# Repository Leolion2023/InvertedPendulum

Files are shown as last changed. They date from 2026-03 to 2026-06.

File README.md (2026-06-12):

# InvertedPendulum
## Concept Idea
A small robot capable of balancing itself so that it remains upright despite having only two wheels.
The motivation behind this is a school project, with the main focus on self-regulating control loops. This robot was our idea for the project.

---

## Language
- Primary Documentation (English): [README.md](README.md)
- German Version: [README.de.md](README.de.md)

---

## Table of Contents

1. [Hardware](#hardware)
   1. [Requirements](#requirements)
   2. [Pinout](#pinout)
   3. [Schematic](#schematic)
   4. [Breadboard](#breadboard)
2. [Software](#software)
   1. [Code](#code)
   2. [Control Loop Diagram](#control-loop-diagram)
   3. [Program Flowchart](#program-flowchart)
3. [Operating Instructions](#operating-instructions)

---

## To Do

- [x] Create a CAD model of the robot
- [x] Make component connections more stable (based on 3 prototypes to ensure maximum reliability, see [Prototypes](/assets/Prototypes.jpg))
- [x] Design for resource efficiency
- [x] Use fewer components for easier assembly and more stable holding
- [x] Fixed sensor mounting on the PCB for stable readings
- [x] Design non-slip tires
- [x] Reuse PCB from an old project to recycle resources
- [x] Write code to keep the robot upright
- [ ] Improve code to enable calibration via smartphone
   - [ ] Connect via BLE to an app **OR**
   - [ ] Open a web server on the local Wi-Fi network
- [ ] Prevent slight tilting
   - Could be related to PID control (unable to compensate for small angles¹)
- [ ] Consider additional parameters in control
   - For example, preventing the robot from covering large distances (or doing so intentionally). Additionally, unintended rotation could be compensated for or controlled.

**Notes:**
1. The code prevents the system from reacting to small angles. However, testing without this hysteresis also failed, as a ~1-2 degree angle only results in a few watts of output to the motor, which is insufficient for compensation. An adjustment should be written to react more aggressively to small values.

## Updates

`
In the first version of the model, the joints were equipped with sliders. These were intended to simplify assembly, but unfortunately it quickly became apparent that they came apart too easily when subjected to even a little too much force. We resolved this issue by designing new joints that were significantly more stable and in which all degrees of freedom were locked in place by a snap-fit mechanism. We also combined various smaller components into larger assemblies, which also provided greater stability. The old versions can be viewed in the Git history. 
`

---

# Hardware
## Requirements

- 2 x geared motors ~600 RPM
   - 2 x M3 screws, 7.3 mm (flat head/countersunk¹)
- ESP32
- BNO055 9DoF Sensor²
- H-Bridge (e.g., HW-095 L298N)
- CAD 3D-printed parts ([see here](TechDrawRework.pdf))³

**Notes:**
1. The screw type depends on the geared motor used.
2. We used this [self-created wiki](https://github.com/Leolion2023/BNO055) because the Bosch documentation is difficult to understand.
3. If you have issues displaying the technical drawing, please download the file and open it in a modern PDF viewer.

---
## Pinout

| ESP32 Pin | Function | Additional Info |
|---|---|---|
| GPIO16 | H-Bridge IN1 | Used for Motor 1 |
| GPIO17 | H-Bridge IN2 | Used for Motor 1 |
| GPIO23 | H-Bridge ENA | Used for Motor 1 (PWM) |
| GPIO18 | H-Bridge IN3 | Used for Motor 2 |
| GPIO19 | H-Bridge IN4 | Used for Motor 2 |
| GPIO33 | H-Bridge ENB | Used for Motor 2 (PWM) |
| GPIO21 | BNO055 SDA | |
| GPIO22 | BNO055 SCL | |
| 3.3V | BNO055 VIN | |
| GND | BNO055 GND | |
| GND | BNO055 ADD | |
| --- | BNO055 INT | *Not used* |
| --- | BNO055 RST | *Not used* |
| --- | BNO055 BOOT | *Not used* |

---
## Schematic
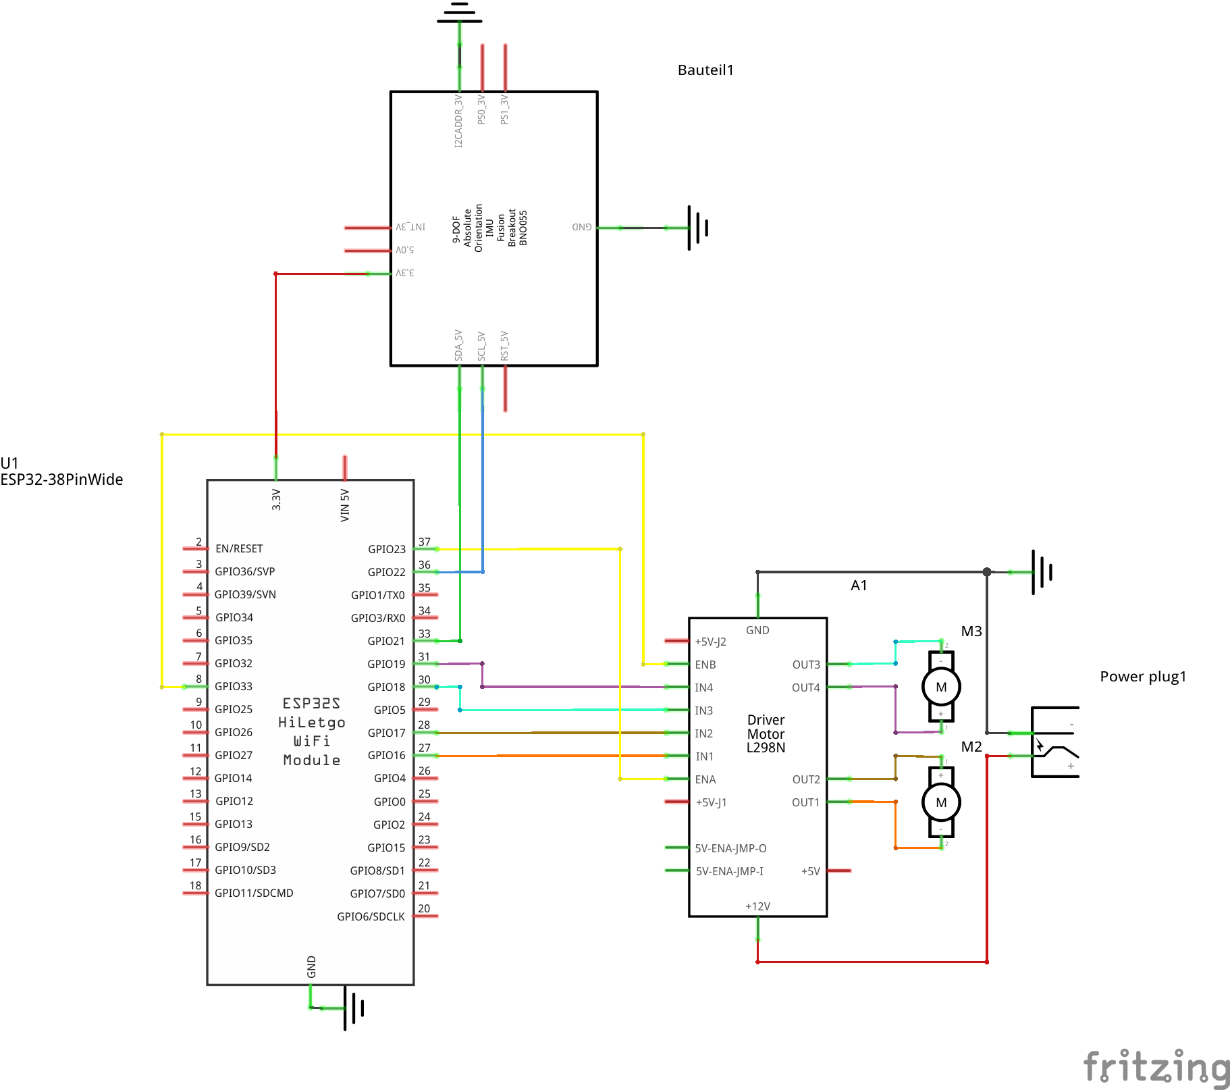
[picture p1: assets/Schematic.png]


---
## Breadboard
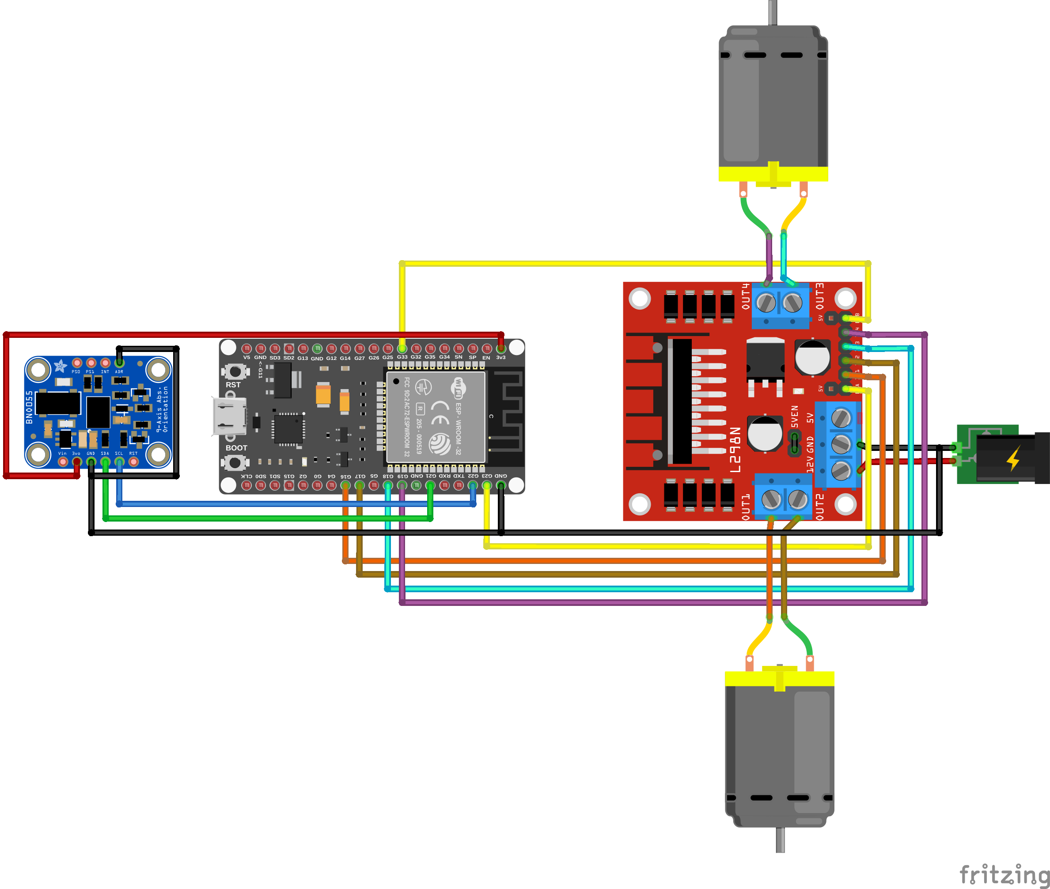
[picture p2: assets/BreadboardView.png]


---
# Software

---
## Code
The main code is located in [src/src/main.cpp](src/src/main.cpp).
We used PlatformIO to flash the ESP32. Adjust as needed to fit your requirements.

---
## Control Loop Diagram
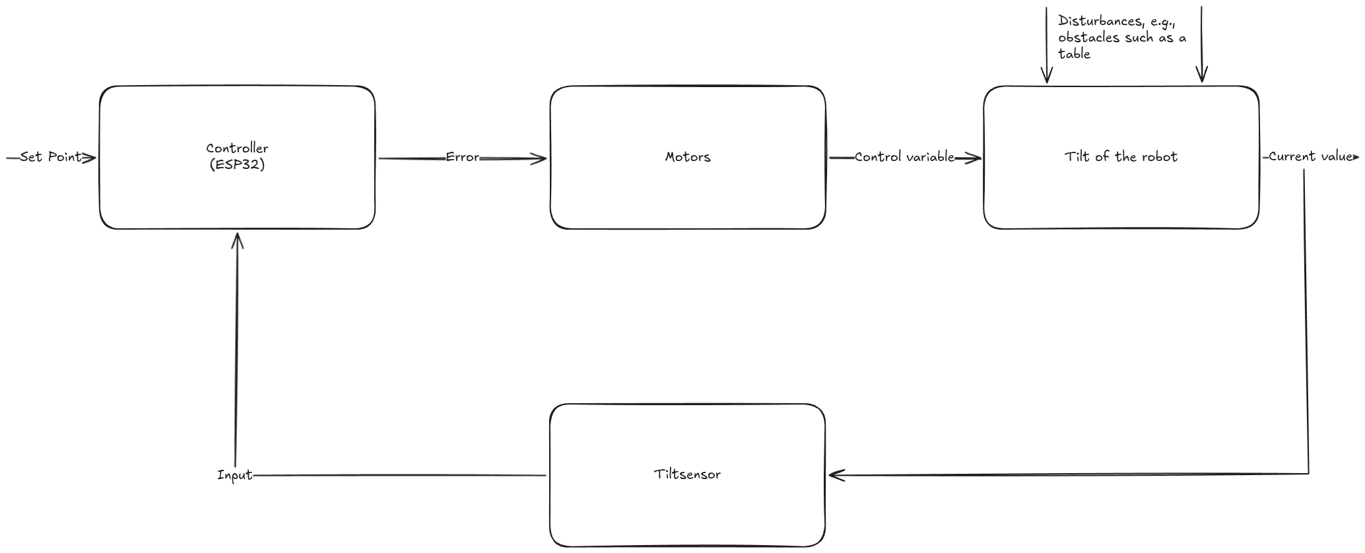
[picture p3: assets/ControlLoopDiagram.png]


---
## Program Flowchart
Currently only available in German.

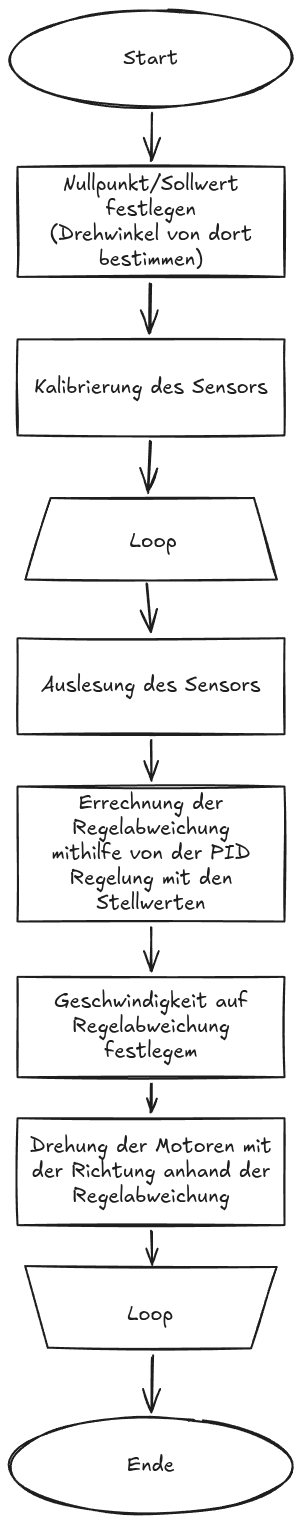
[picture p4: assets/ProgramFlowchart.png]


**Both diagrams were created using [excalidraw.com](https://excalidraw.com).**

---
# Operating Instructions

---
### Electrical Startup

The robot requires two separate power supplies: one for logic voltage and one for motor voltage. The logic voltage can be provided via the ESP32’s USB-C port, the VIN pin (3.3V–5V), or the 3.3V pin. However, we recommend using the connector on the PCB directly next to the ESP32. The motor voltage must be connected either directly to the H-Bridge at the 12V and GND terminals or to the main power supply on the PCB.

Since you will likely need to calibrate the PID values, the easiest way is to connect the ESP32 to a computer with either PlatformIO or the Arduino IDE installed:

**For PlatformIO:**
1. Install PlatformIO on your laptop/PC/etc.
2. Install the custom library for BNO055 (linked above) or the official Bosch library (no guarantee of updates).
3. Adjust the code as described in the next section.
4. Place the robot on a level surface so the wheels are not touching the ground (for initial calibration).
5. Connect the ESP32 and upload the code.

**For Arduino IDE:**
1. Install Arduino IDE.
2. Install the library ([either via Arduino Library Manager or as a file](https://docs.arduino.cc/software/ide-v1/tutorials/installing-libraries/)).
3. Adjust the code as described in the next section.
4. Place the robot on a level surface so the wheels are not touching the ground (for initial calibration).
5. Connect the ESP32 and upload the code.

---
### Code Adjustments

There are a few simple adjustments to be made. At the top, you’ll find the three PID constants, which need to be tuned for your robot. The `constraint` limits the maximum output of the PID controller. Typically, 255.0 is reasonable, as it is the maximum PWM value. The `minConstraint` prevents the motors from spinning at low power, as rapid toggling of the power supply can damage the motors. The `inverted` variable controls the motor rotation direction. If the robot regulates in the wrong direction, change it to `-1.0` or `1.0`.

---
### Hardware Information

To build the robot, you can simply use the technical drawings. Minor adjustments to the variables in the CAD files can improve the connections but may also introduce errors.

**Notes:**
1. We currently have the motors connected in parallel to one channel of the H-Bridge, as they otherwise rotated differently. This could also be balanced by code that reads the other dimensions of the BNO055 and attempts to prevent rotation.

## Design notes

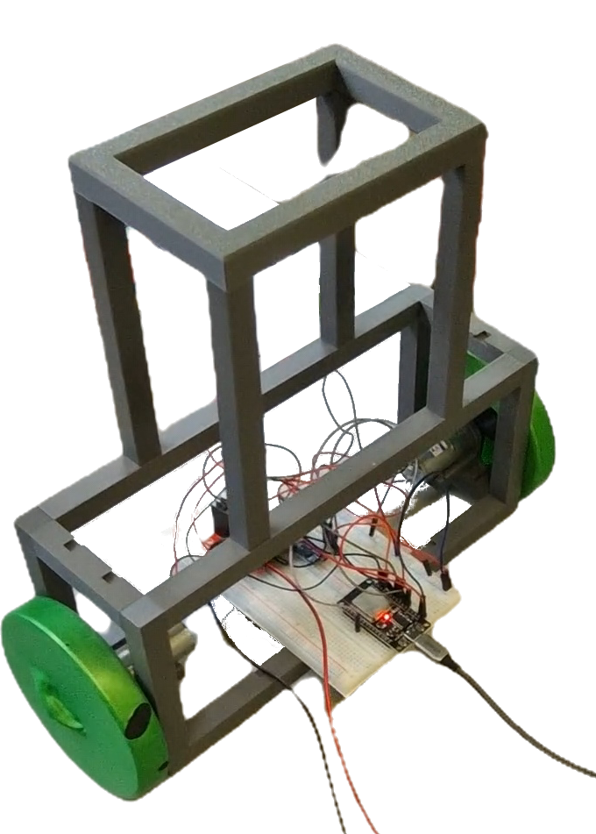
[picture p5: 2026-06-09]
assets/MK1.png

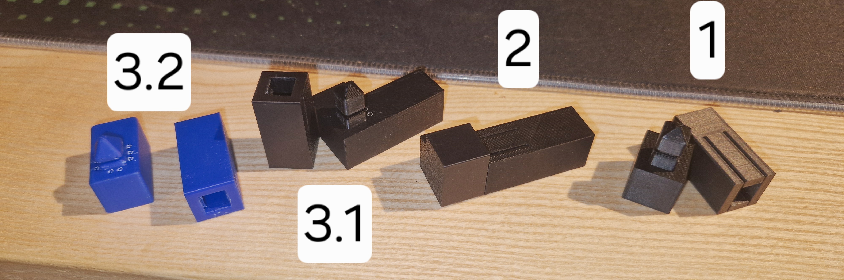
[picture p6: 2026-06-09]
assets/Prototypes.jpg

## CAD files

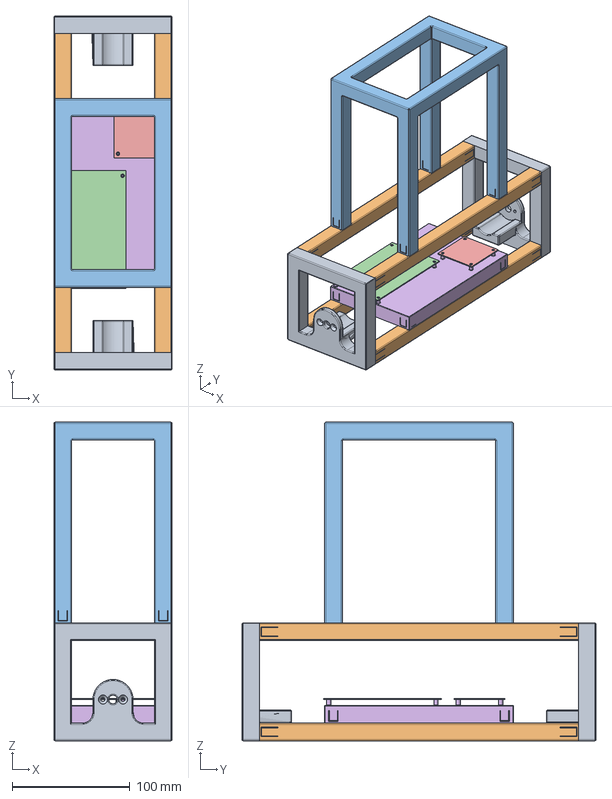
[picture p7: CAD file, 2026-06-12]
CAD/NewSetup.FCStd
100.0 x 300.0 x 270.0 mm
SidePanel001 x 2
Beam001 x 4
Top
PCB
L298N
PCBHolder

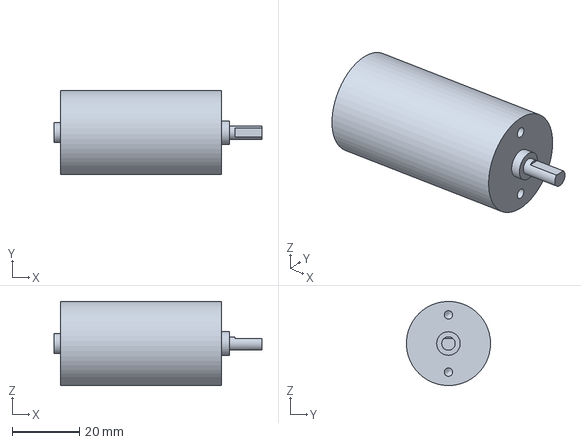
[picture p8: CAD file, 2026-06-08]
CAD/DCMotor.FCStd
61.8 x 25.0 x 25.0 mm

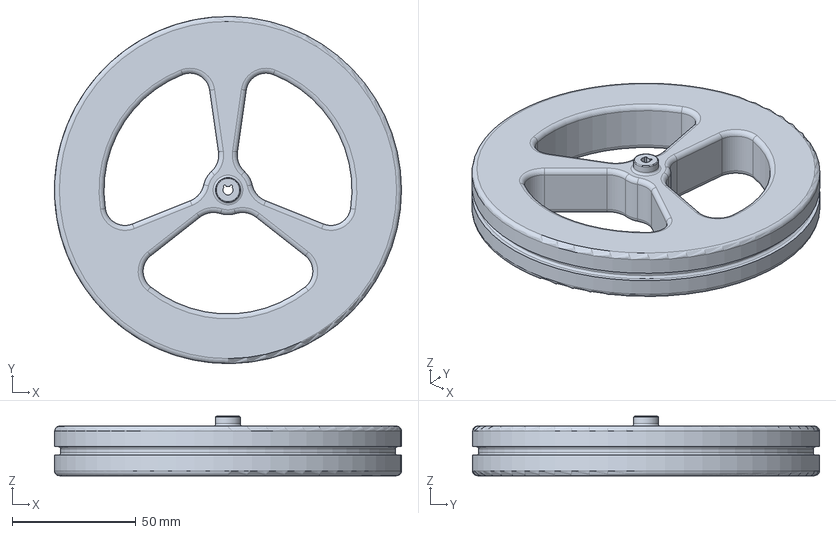
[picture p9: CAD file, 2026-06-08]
CAD/Wheel.FCStd
140.0 x 140.0 x 24.0 mm

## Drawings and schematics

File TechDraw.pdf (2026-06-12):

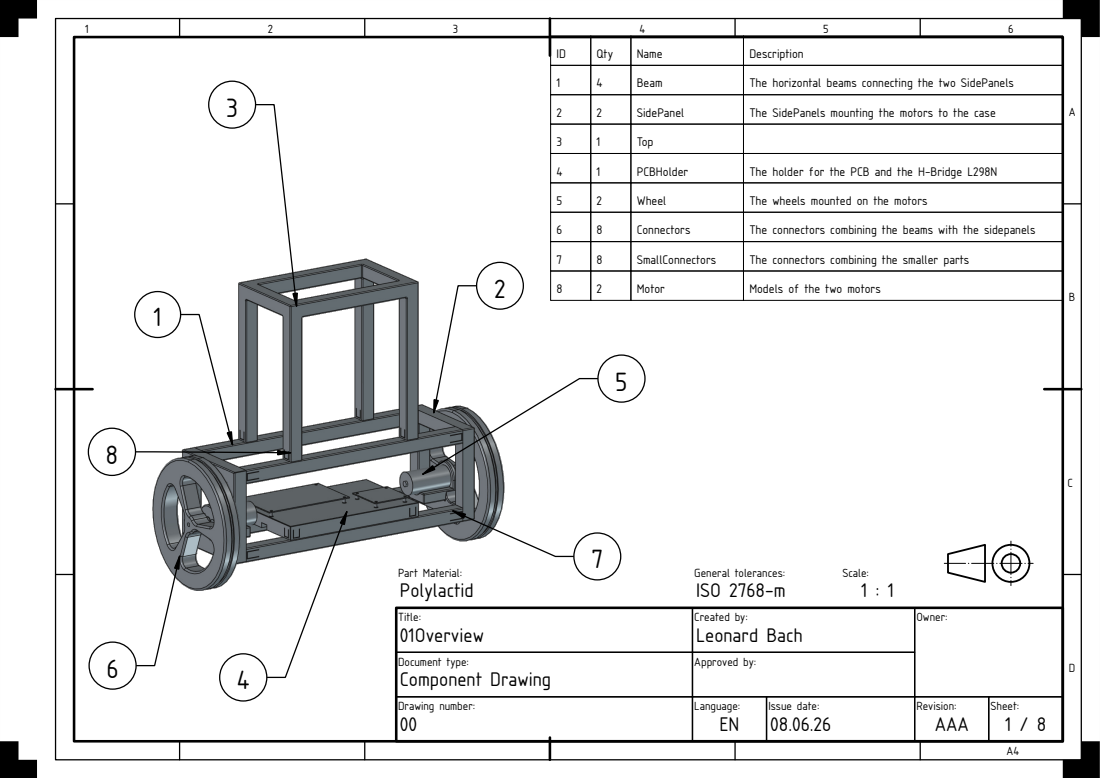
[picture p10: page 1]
Part Material:; General tolerances:; Scale:; Polylactid; ISO 2768-m

ID | Qty | Name | Description
1 | 4 | Beam | The horizontal beams connecting the two SidePanels
2 | 2 | SidePanel | The SidePanels mounting the motors to the case
3 | 1 | Top
4 | 1 | PCBHolder | The holder for the PCB and the H-Bridge L298N
5 | 2 | Wheel | The wheels mounted on the motors
6 | 8 | Connectors | The connectors combining the beams with the sidepanels
7 | 8 | SmallConnectors | The connectors combining the smaller parts
8 | 2 | Motor | Models of the two motors

Title: 01Overview | Created by: Leonard Bach | Owner:

Document type: Component Drawing | Approved by:

Drawing number: 00 | Language: EN | Issue date: 08.06.26 | Revision: AAA | Sheet: 1 / 8

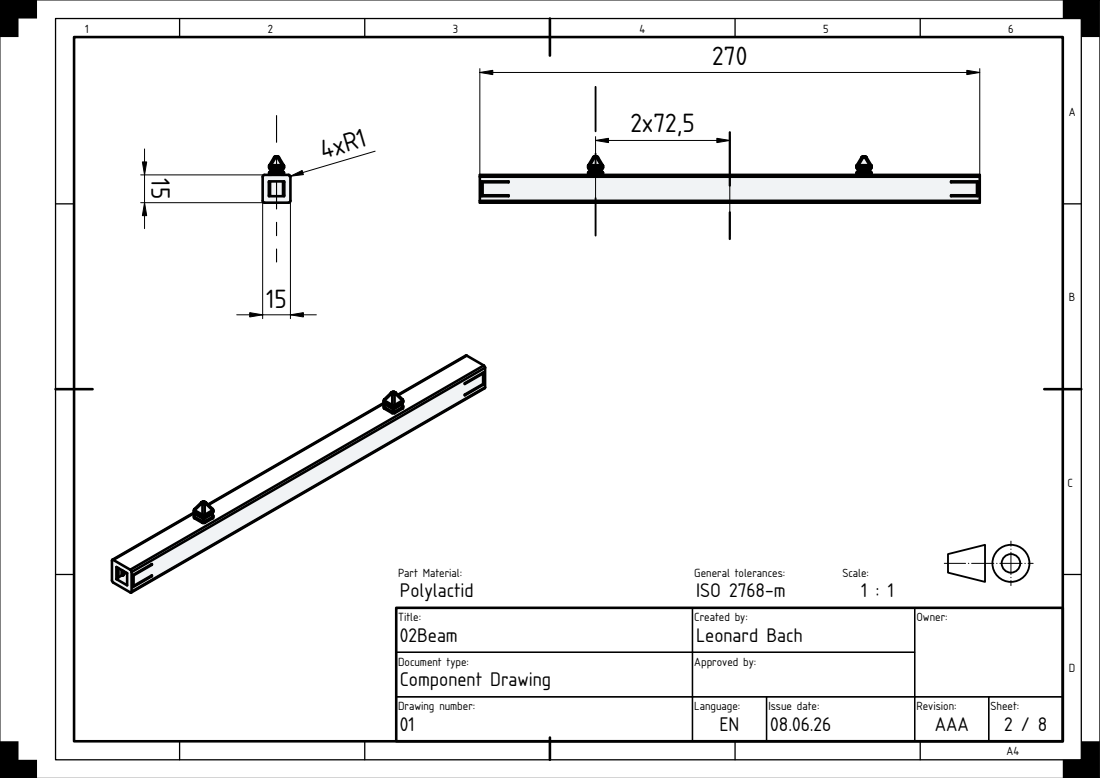
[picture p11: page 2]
Part Material:; General tolerances:; Scale:; Polylactid; ISO 2768-m

Title: 02Beam | Created by: Leonard Bach | Owner:

Document type: Component Drawing | Approved by:

Drawing number: 01 | Language: EN | Issue date: 08.06.26 | Revision: AAA | Sheet: 2 / 8

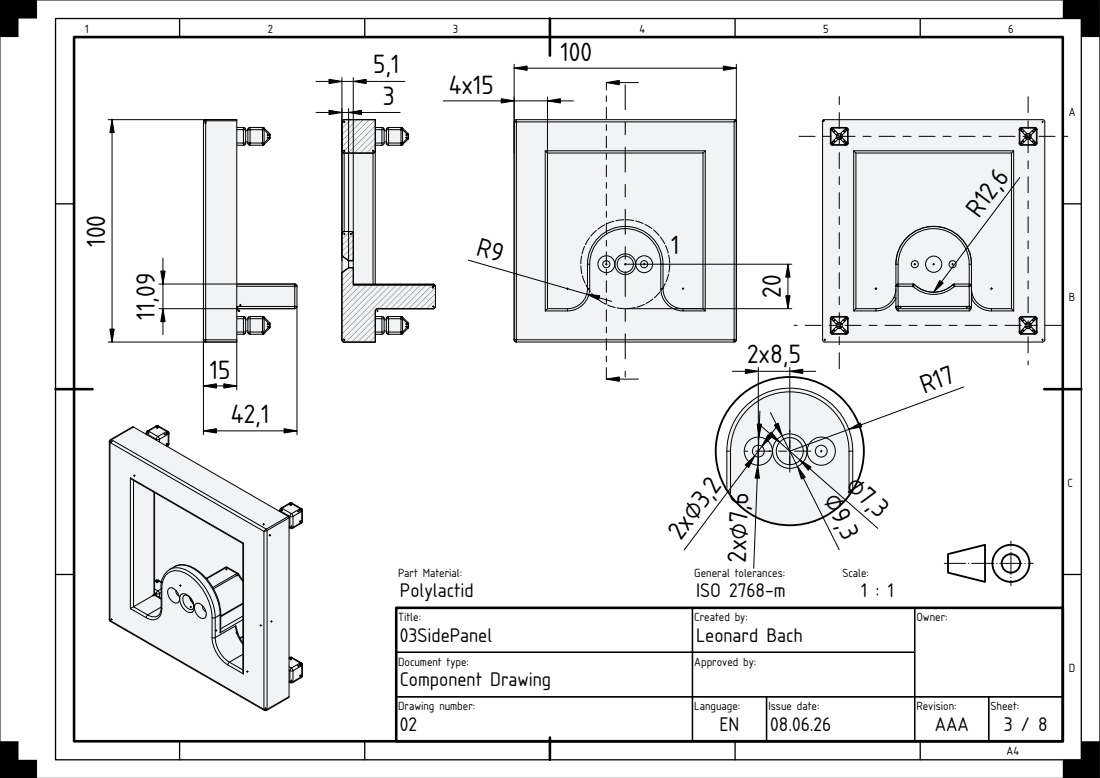
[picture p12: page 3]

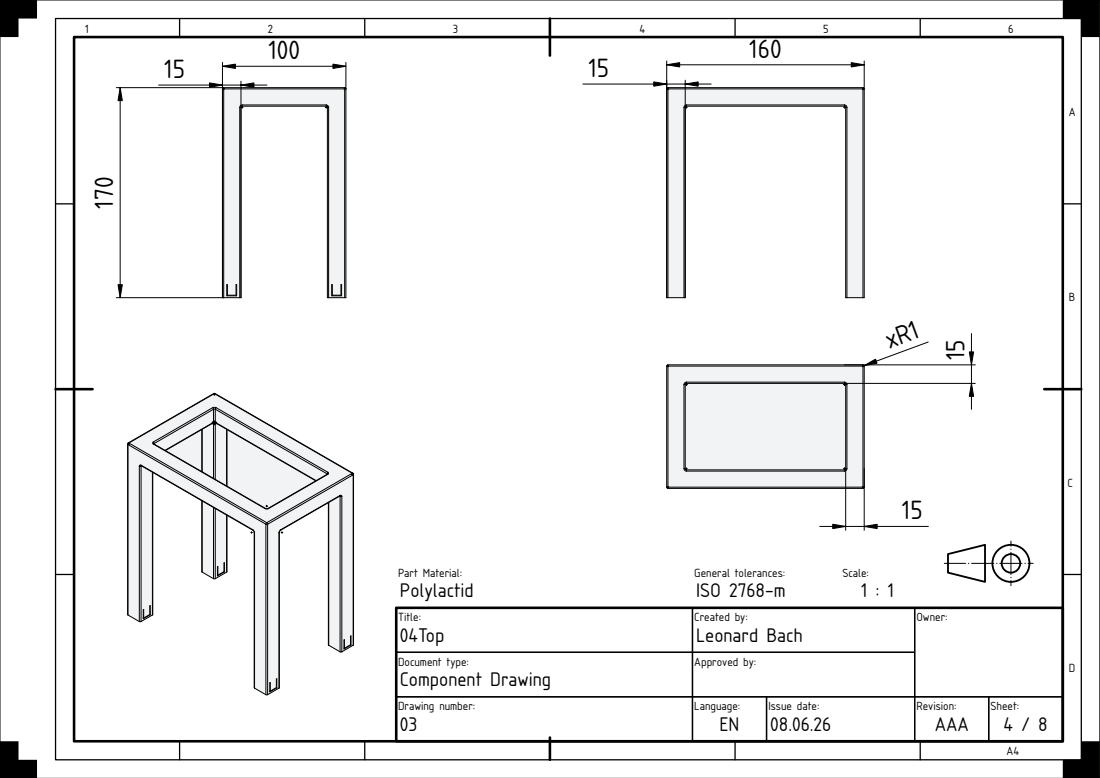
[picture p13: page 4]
Part Material:; General tolerances:; Scale:; Polylactid; ISO 2768-m

Title: 04Top | Created by: Leonard Bach | Owner:

Document type: Component Drawing | Approved by:

Drawing number: 03 | Language: EN | Issue date: 08.06.26 | Revision: AAA | Sheet: 4 / 8

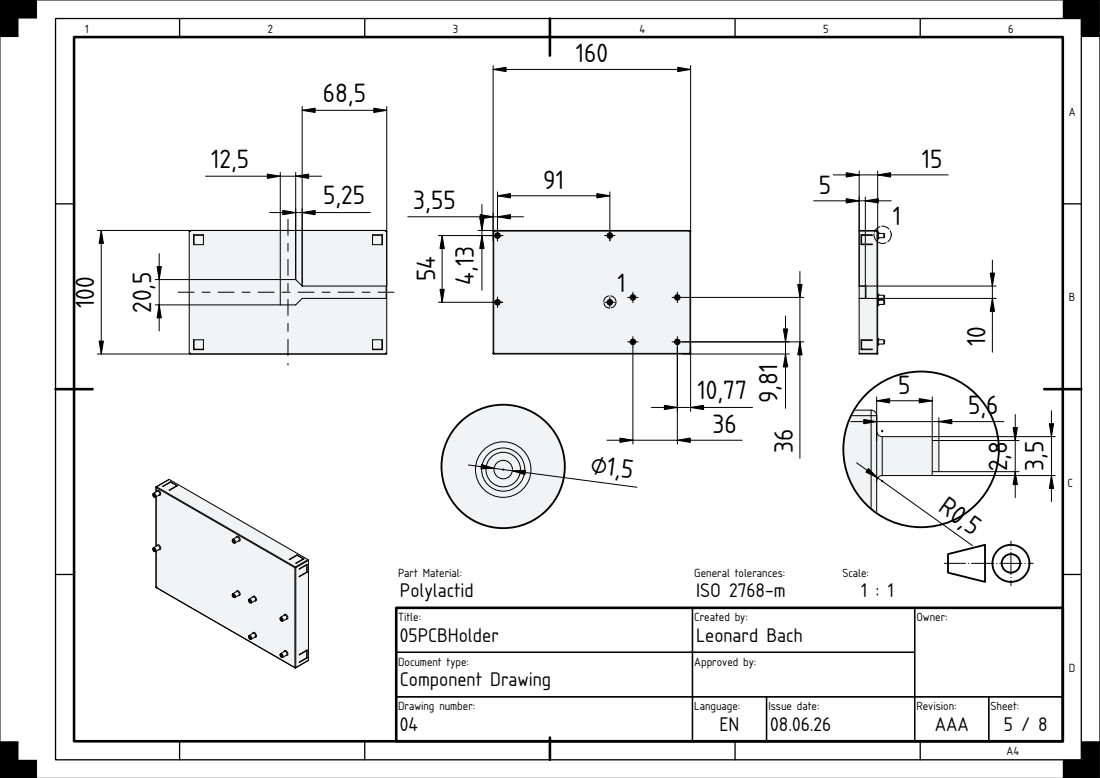
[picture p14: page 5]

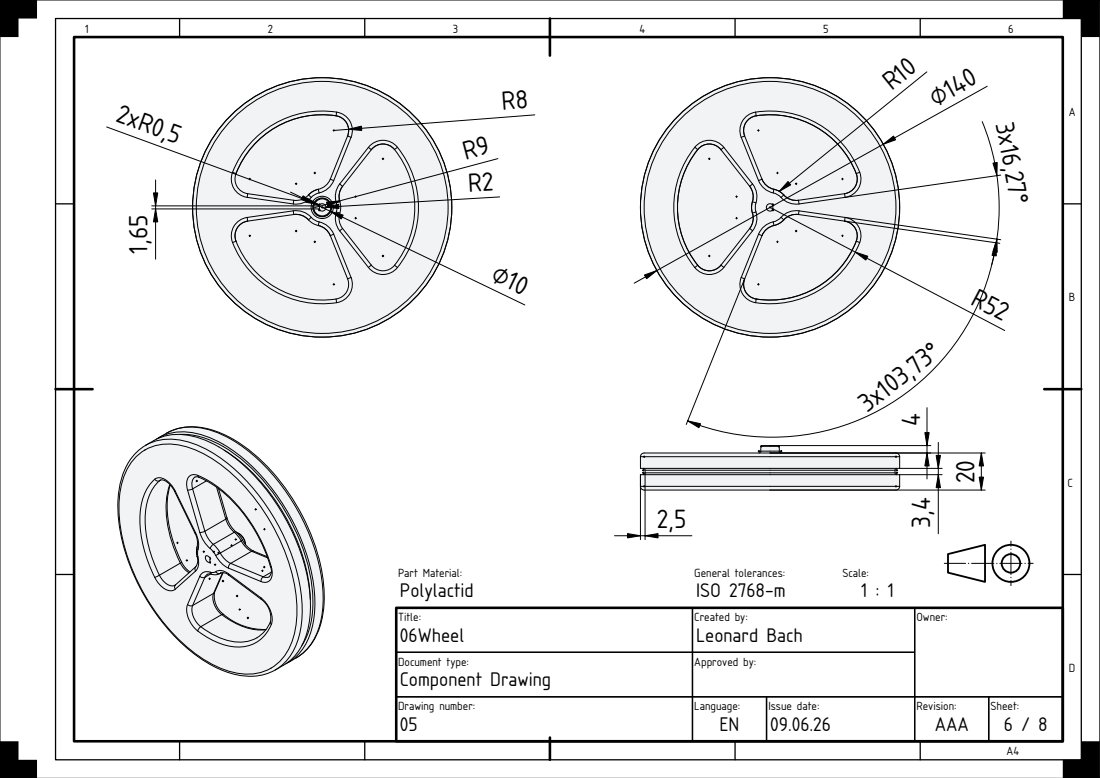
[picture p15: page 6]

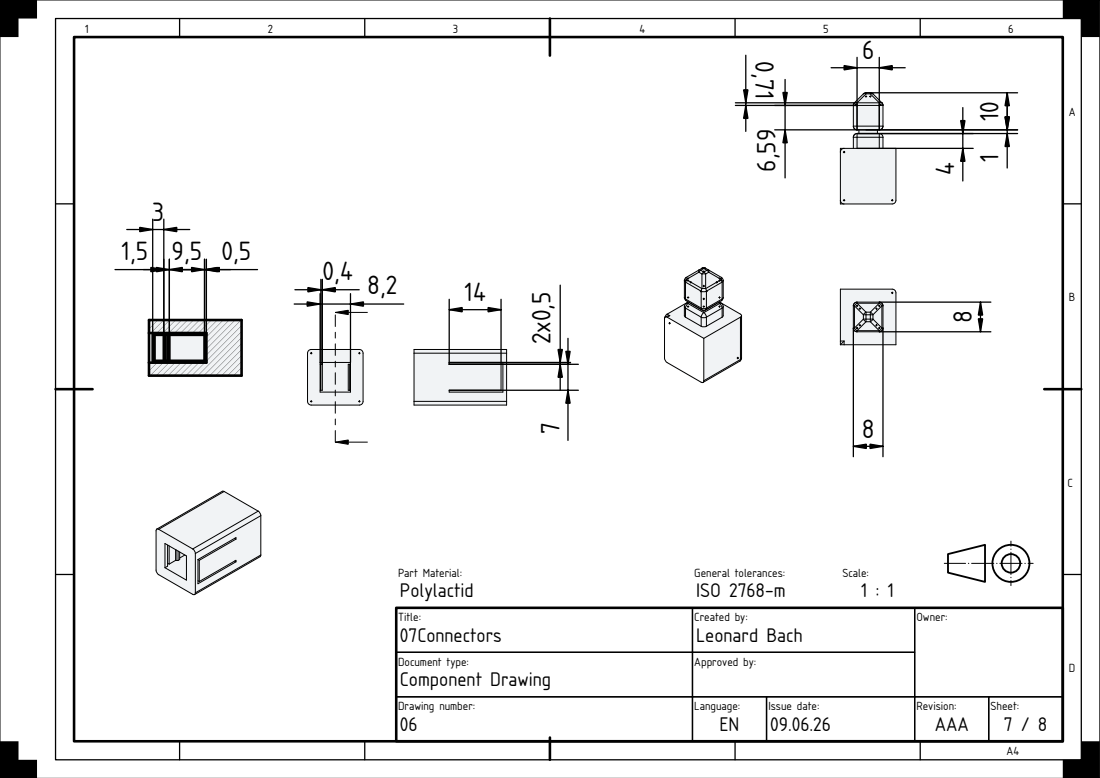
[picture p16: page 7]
Part Material:; General tolerances:; Scale:; Polylactid; ISO 2768-m

Title: 07Connectors | Created by: Leonard Bach | Owner:

Document type: Component Drawing | Approved by:

Drawing number: 06 | Language: EN | Issue date: 09.06.26 | Revision: AAA | Sheet: 7 / 8

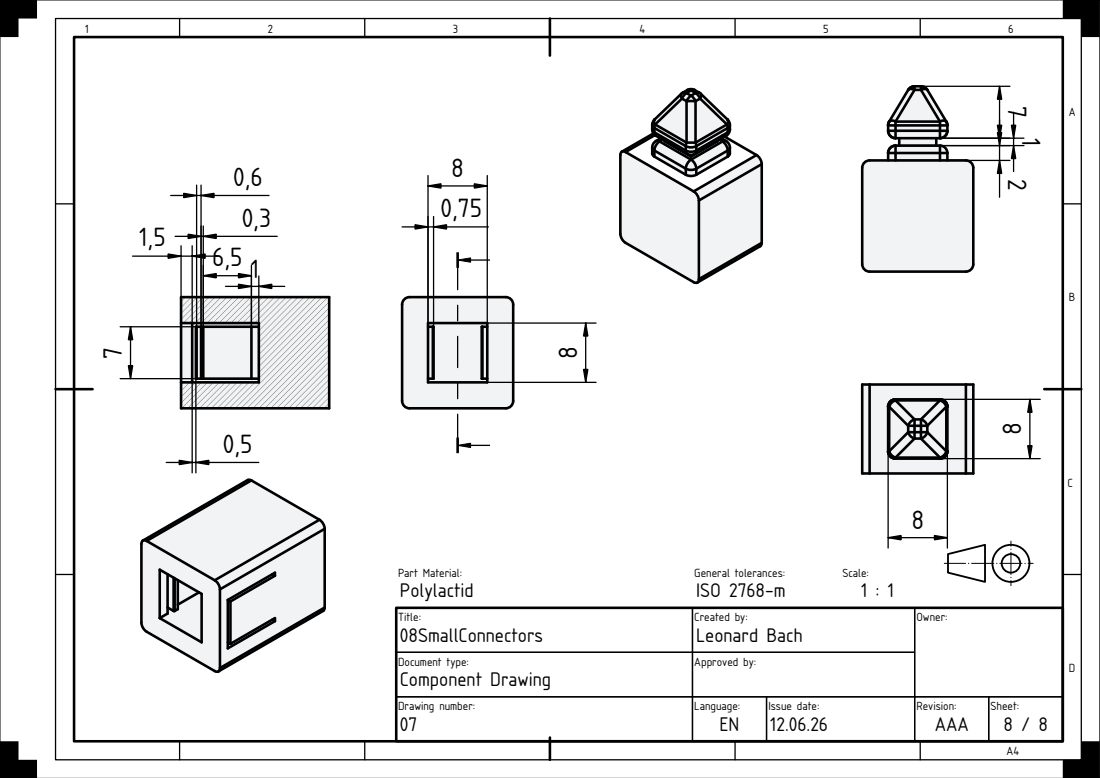
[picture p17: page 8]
Part Material:; General tolerances:; Scale:; Polylactid; ISO 2768-m

Title: 08SmallConnectors | Created by: Leonard Bach | Owner:

Document type: Component Drawing | Approved by:

Drawing number: 07 | Language: EN | Issue date: 12.06.26 | Revision: AAA | Sheet: 8 / 8

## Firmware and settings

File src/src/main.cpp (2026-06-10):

#include "BNO055_support.h"
#include "BNO055.h"
#include <Wire.h>

// Define PID constants
#define kP 20.0
#define kI 2.0
#define kD 2.0

#define inverted 1.0 // Variable to control motor direction, can be set to -1.0 to invert controls
#define constraint 255.0 // Maximum absolute value for PID output, used to constrain motor speeds
#define min_constraint 0.0 // Minimum constraint to ensure motors receive enough power to move

// Define motor control pins
#define IN1 16
#define IN2 17
#define IN3 18
#define IN4 19
#define PWMA 23
#define PWMB 33

struct bno055_t myBNO;
struct bno055_euler euler;

// Define global variables
float prev_error = 0.0;
float zero_point = 0.0;
float time_step = 0.01; // Time step for PID calculations (10 ms)

/** 
 * @brief Calculates the PID output based on the current error and time step
 * @param constraints The maximum absolute value for the PID output, used to constrain motor speeds
 * @return The calculated PID output, which is constrained as it is used with pwm for motor control
 */
float pid_calc(float constraints) {
  // Calculation of the different PID components based on the current error and time step

  // Calculate the error between the current angle and the zero point, 
  // where euler.p is the pitch angle in degrees multiplied by 16 (as per BNO055 specifications)
  float error = (euler.p / 16.0) - zero_point;
  // Calculate the different PID components
  float P = kP * error;
  float I = kI * error * time_step;
  float D = kD * (error - prev_error) / time_step; 
  float output = P + I + D;
  prev_error = error;
  // Constrain the PID output to prevent excessive motor speeds
  output = constrain(output, -constraints
  , constraints
  );
  return output;
}

void setup() {
  // Initialize I2C and serial communication
  Wire.begin();
  Serial.begin(115200);

  // Set motor control pins as outputs
  pinMode(IN1, OUTPUT);
  pinMode(IN2, OUTPUT);
  pinMode(IN3, OUTPUT);
  pinMode(IN4, OUTPUT);
  pinMode(PWMA, OUTPUT);
  pinMode(PWMB, OUTPUT);


  // Initialize BNO055 sensor
  BNO_Init(&myBNO);
  bno055_set_operation_mode(OPERATION_MODE_NDOF); // Set the sensor to NDOF mode for full sensor fusion
  delay(600); // Allow time for sensor to initialize


 // Wait for full calibration (all sensors must reach 3)
  

  // Read initial Euler angles to establish zero point
  bno055_read_euler_hrp(&euler);

  zero_point = euler.p / 16.0;
  Serial.println((String)"Zero Point: " + zero_point);
  
  for (int i = 5000; i > 0; i -= 1000) {
    Serial.println((String)"Starting in " + i / 1000 + " seconds...");
    delay(1000);
  }
}
void loop() {
  // Read current Euler angles from the sensor
  bno055_read_euler_hrp(&euler);
  float error = pid_calc(constraint); // Calculate the PID error based on the current pitch angle and zero point
  float motor_speed = error * inverted; // Calculate motor speed based on PID control, invert if necessary
  float sign = (motor_speed >= 0) ? 1 : -1; // Determine the direction of motor control
  motor_speed = abs(motor_speed); // Use the absolute value of the motor speed for PWM control
  // Set motor speeds using PWM
  if (motor_speed < min_constraint) {
    motor_speed = min_constraint; // Ensure motors receive enough power to move
  }
  analogWrite(PWMA, motor_speed);
  analogWrite(PWMB, motor_speed);
  // Serial.println((String)"Error: " + error + " | Motor Speed: " + motor_speed);
  // Control motor direction based on the sign of the PID error
  if (error >= 0 && error <= 0) { // If the error is small, stop the motors
    digitalWrite(IN1, LOW);
    digitalWrite(IN2, LOW);
    digitalWrite(IN3, LOW);
    digitalWrite(IN4, LOW);
  }
  else if (error > 0) {
    digitalWrite(IN1, HIGH);
    digitalWrite(IN2, LOW);
    digitalWrite(IN3, LOW);
    digitalWrite(IN4, HIGH);
  }
  else if (error < 0) {
    digitalWrite(IN1, LOW);
    digitalWrite(IN2, HIGH);
    digitalWrite(IN3, HIGH);
    digitalWrite(IN4, LOW);
  } 
  delay(time_step);
}

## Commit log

2025-12-17 Added ProjectManagement file
    [Projektmanagement_Gantt-Diagramm.xlsx]
2026-01-13 Add CAD Files
    [0.+Corner+bracket+for+2020+aluminum+profiles+-+M5+screw+-+Whole+Set+(V2).3mf, DCMotor.FCStd, Entwurf.FCStd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]
2026-01-13 Some changes to the CAD
    [0.+Corner+bracket+for+2020+aluminum+profiles+-+M5+screw+-+Whole+Set+(V2).3mf, Entwurf2.FCStd, Profile.FCStd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]
2026-01-14 Add new Idea
    [Entwurf2.FCStd]
2026-02-10 Udpate CAD and Readme.md
    [DCMotor.FCStd, Entwurf2.FCStd, MotorAttachment.FCStd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]
2026-02-10 Add new CAD Files
    [DCMotor.FCStd, Entwurf2.FCStd, MotorAttachment.FCStd]
2026-02-25 Added example codes
    [Entwurf2.FCStd]
2026-03-27 Adding current status
    [Assembly.FCStd, DCMotor.FCStd, Entwurf2.FCStd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]
2026-03-29 Pushing some CAD updates and assets
    [Assembly.FCStd, DCMotor.FCStd, MotorAttachment.FCStd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]
2026-03-29 Updating CAD and README and else
    [Assembly.FCStd, DCMotor.FCStd, InvertedPendulum.fzz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]
2026-03-29 Updating some things
    [Projektmanagement_Gantt-Diagramm.xlsx, TechDraw.FCStd]
2026-03-29 Update Gantt diagram
    [Projektmanagement_Gantt-Diagramm.xlsx]
2026-03-30 Updating CAD and creating TechnDraw
    [Assembly.FCStd, DCMotor.FCStd, MotorAttachment.FCStd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]
2026-06-08 Update CAD files
    [Assembly.FCStd, DCMotor.FCStd, MotorAttachment.FCStd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]
2026-06-08 Remove old CAD Files not needed anymore
    [Assembly.FCStd, Entwurf.FCStd, MotorAttachment.FCStd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]
2026-06-08 Add new TechDraw currently not finished
2026-06-09 Update TechDrawing in NewSetup
    [NewSetup.FCStd]
2026-06-12 Update TechDraw
    [NewSetup.FCStd]
